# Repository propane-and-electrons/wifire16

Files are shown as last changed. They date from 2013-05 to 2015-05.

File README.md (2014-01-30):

wifire16
--------

After I wired up 16 MOSFET + optoisolator circuits on perfboard for Flux and Fire, I swore I was never going to do it by hand again. When it came time to make a similar circuit for Super Street Fire, I decided the only option was to make a PCB to wirelessly control 16 flame effects. The end result: the wifire16 board.

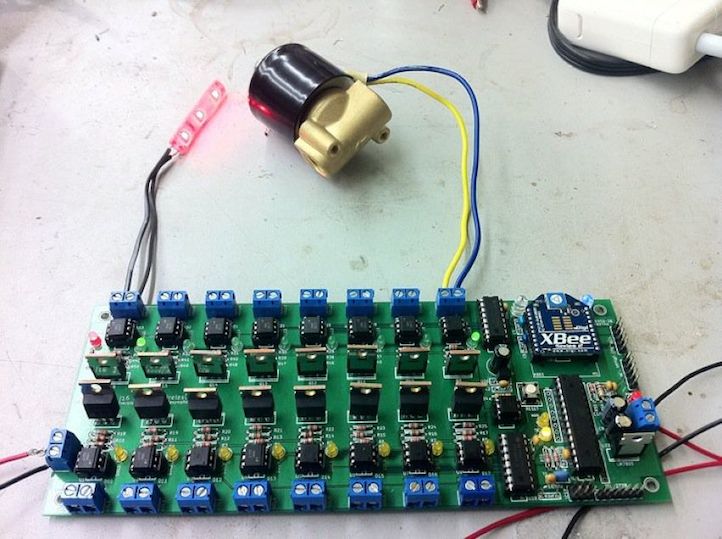
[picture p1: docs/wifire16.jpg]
wifire16 photo


### Feature Summary

* Arduino compatible
* Programmable via 6-pin FTDI header or 6-pin ICSP header
* 16 PWM-capable DC load channels switched via MOSFET
* Wireless support with XBee or compatible radio, e.g. RN-XV WiFly
* All ATMega I/O pins are broken out on the board
* DC load power is optoisolated from the control system power
* Power connectors use 5mm screw terminals or Anderson Powerpole connectors
* Load power status is reported to the microcontroller via an optoisolated input pin
* Output power channels are controlled with a TLC5940 constant current driver that works like a shift register
* Each output channel has a status LED for easy debugging
* TLC5940 control lines are broken out to input/output headers, so boards can be chained without additional control systems

### Design

The wifire16 takes two power inputs: 7-12 volts for the control side, and anything (within reason, e.g. 12 or 24 volts) for the load side. The control system acts exactly like an Arduino with attached XBee/WiFly radio, and is electrically optoisolated from the load side.The independent microcontroller (ATMega328P) on the board can control the power output channels via a pre-programmed routine, interactively over a wireless link, or with external sensors attached to the I/O pins. If more than 16 channels are needed, multiple boards can be chained together and controlled in the same way, with only one control system necessary.

The original purpose of the wifire16 is to control DC-powered solenoid valves for flame effects. The isolation of the two power sources protects the control side from the higher voltage load side, and also allows the load side power to be cut (i.e. by an arming or deadman switch) without affecting the control system. While the system was intended to handle solenoid valves that require 1A+ per channel, it can also be used to control anything else that needs DC power, e.g. motors or 12v LED rope lighting.

### v1 Note

The deprecated v1 version of this board used regular 74595 shift registers and were not PWM capable on all output channels. It also did not have Anderson Powerpole connnectors.

### Documents

* [Schematic](docs/wifire16-schematic.pdf)
* [Bill of Materials](docs/wifire16-BOM.csv)

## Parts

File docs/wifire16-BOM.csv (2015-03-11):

Designator | Package | Quantity | Part | Digi-Key Part
C1,C2,C3,C4,C6,C11 | C2 | 6 | 0.1uF | 490-5388-ND
C5 | C1V8 | 1 | 100uF | P13459-ND
C7,C12,C13 | C2 | 3 | 1uF | 445-2858-ND
C8 | C2 | 1 | 8.2pF | 490-3764-ND
C9,C10 | C1V5 | 2 | 47uF | P13464-ND
D2,D4,D6,D8,D10,D12,D14,D16,D18,D20,D22,D24,D26,D28,D30,D32,D33 | LED-3MM | 17 | LED 3mm (red) | 754-1606-ND
D1,D3,D5,D7,D9,D11,D13,D15,D17,D19,D21,D23,D25,D27,D29,D31,D34 | D3 | 17 | 1N4004 | 641-1311-1-ND
D35,D36,D37 | LED-3MM | 3 | LED 3mm (green) | 754-1603-ND
JP1,JP2,P20 | SIL-2, SIL-6 | 10 | header pins | A34253-40-ND
M1 | XBEE | 1 | RN-XV | 740-1044-ND
P1-P17,P27 | PP-2H-5MMSCREWTERM | 18 | 5mm screw terminals or Anderson Powerpole connectors | ED2600-ND
P21 | pin_array_3x2 | 3 | 2x header pins | A34344-40-ND
Q1-Q17 | TO220GDS_VERT | 16 | IRF510 | IRF510PBF-ND
R1,R3,R5,R7,R9,R11,R13,R15,R17,R19,R21,R23,R25,R27,R29,R31,R36 | R3 | 17 | 10k | 10KQBK-ND
R2,R4,R6,R8,R10,R12,R14,R16,R18,R20,R22,R24,R26,R28,R30,R32,R34,R37,R38,R39 | R3 | 20 | 1k | 1.0KQBK-ND
R33 | R3 | 1 | 2.2k | 2.2QBK-ND
R35 | R3 | 1 | 4k | not in stock?!
SW1 | SW-6MM-4PIN | 1 | momentary pushbutton | SW400-ND
U1-U17 | DIP-6__300 | 17 | 4N35 | 516-1557-5-ND
U18 | DIP-28__300 | 1 | TLC5940 | 296-17732-5-ND
U19 | SIL-3 | 1 | MCP1700 | MCP1700-3302E/TO-ND
U20 | DIP-14__300 | 1 | 74AHC125 | 296-4531-5-ND
U21 | 7805 | 1 | LM7805 | LM7805CT-ND
U22 | DIP-28__300 | 1 | ATMEGA328 | ATMEGA328P-PU-ND
U23 | SIL-3 | 1 | MCP1702 | MCP1702-1502E/TO-ND
XM1A,XM1B |  | 2 | 10pin 2mm header | S5751-10-ND
XU1-XU17 | 6-DIP | 17 | 6-DIP socket | A100203-ND
Y1 | SIL-3 | 1 | 16MHz | 490-1214-ND

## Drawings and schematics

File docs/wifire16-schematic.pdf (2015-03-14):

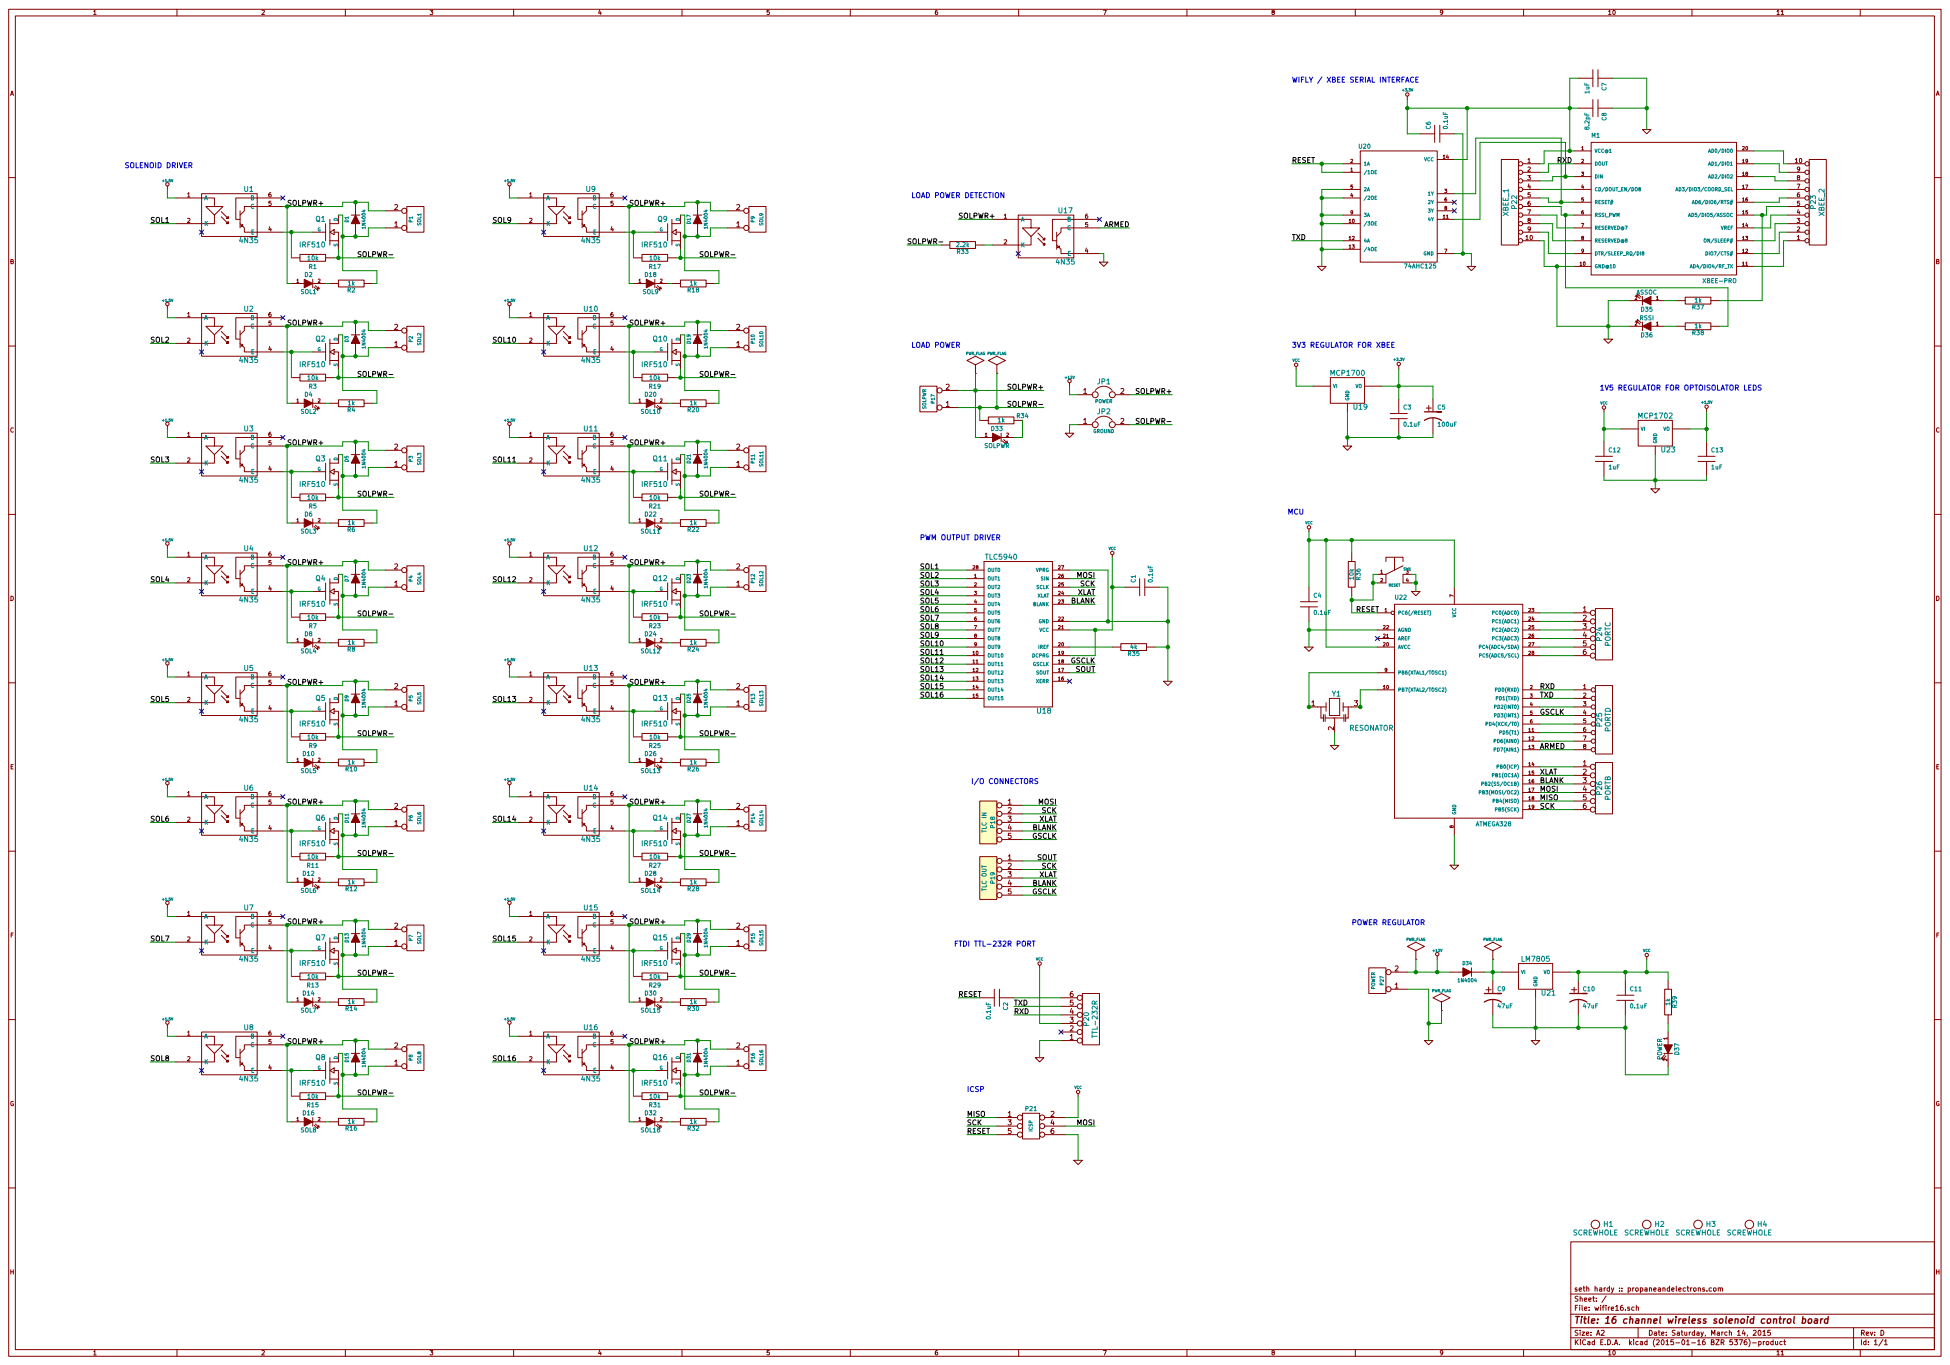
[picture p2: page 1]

WIFLY / XBEE SERIAL INTERFACE

1V5 REGULATOR FOR OPTOISOLATOR LEDS

H4 SCREWHOLE H3 SCREWHOLE H2 SCREWHOLE H1 SCREWHOLE

File: wifire16.sch Sheet: / seth hardy :: propaneandelectrons.com

Id: 1/1 Title: 16 channel wireless solenoid control board

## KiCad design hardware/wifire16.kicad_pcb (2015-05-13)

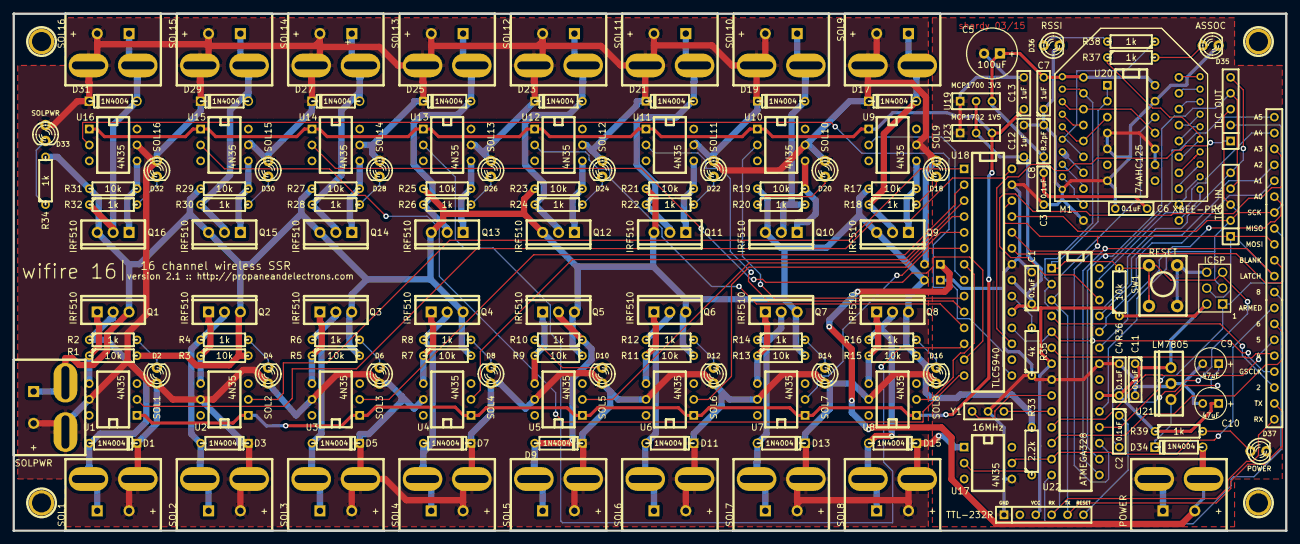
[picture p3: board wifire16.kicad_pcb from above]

Board: 2 copper layers, 203.2 x 82.5 mm, 164 parts (0 on the bottom side), 120 nets.

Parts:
C1, C2, C3, C4, C6, C11: 0.1uF; C2
C5: 100uF; C1V8
C7, C12, C13: 1uF; C2
C8: 8.2pF; C2
C9, C10: 47uF; C1V5
D1, D3, D5, D7, D9, D11, D13, D15, D17, D19, D21, D23, D25, D27, D29, D31, D34: 1N4004; D3
D2: SOL1; LED-3MM
D4: SOL2; LED-3MM
D6: SOL3; LED-3MM
D8: SOL4; LED-3MM
D10: SOL5; LED-3MM
D12: SOL6; LED-3MM
D14: SOL7; LED-3MM
D16: SOL8; LED-3MM
D18: SOL9; LED-3MM
D20: SOL10; LED-3MM
D22: SOL11; LED-3MM
D24: SOL12; LED-3MM
D26: SOL13; LED-3MM
D28: SOL14; LED-3MM
D30: SOL15; LED-3MM
D32: SOL16; LED-3MM
D33: SOLPWR; LED-3MM
D35: ASSOC; LED-3MM
D36: RSSI; LED-3MM
D37: POWER; LED-3MM
H1, H2, H3, H4: SCREWHOLE; 1pin
JP1: POWER; SIL-2
JP2: GROUND; SIL-2
M1: XBEE-PRO; XBEE
P1: SOL1; PP-2H-5MMSCREWTERM
P2: SOL2; PP-2H-5MMSCREWTERM
P3: SOL3; PP-2H-5MMSCREWTERM
P4: SOL4; PP-2H-5MMSCREWTERM
P5: SOL5; PP-2H-5MMSCREWTERM
P6: SOL6; PP-2H-5MMSCREWTERM
P7: SOL7; PP-2H-5MMSCREWTERM
P8: SOL8; PP-2H-5MMSCREWTERM
P9: SOL9; PP-2H-5MMSCREWTERM
P10: SOL10; PP-2H-5MMSCREWTERM
P11: SOL11; PP-2H-5MMSCREWTERM
P12: SOL12; PP-2H-5MMSCREWTERM
P13: SOL13; PP-2H-5MMSCREWTERM
P14: SOL14; PP-2H-5MMSCREWTERM
P15: SOL15; PP-2H-5MMSCREWTERM
P16: SOL16; PP-2H-5MMSCREWTERM
P17: SOLPWR; PP-2H-5MMSCREWTERM
P18: TLC IN; SIL-5
P19: TLC OUT; SIL-5
P20: TTL-232R; SIL-6
P21: ICSP; pin_array_3x2
P22: XBEE_1; SIL-10
P23: XBEE_2; SIL-10
P24: PORTC; SIL-6
P25: PORTD; SIL-8
P26: PORTB; SIL-6
P27: POWER; PP-2H-5MMSCREWTERM
Q1, Q2, Q3, Q4, Q5, Q6, Q7, Q8, Q9, Q10, Q11, Q12, Q13, Q14, Q15, Q16: IRF510; TO220GDS_VERT
R1, R3, R5, R7, R9, R11, R13, R15, R17, R19, R21, R23, R25, R27, R29, R31, R36: 10k; R3
R2, R4, R6, R8, R10, R12, R14, R16, R18, R20, R22, R24, R26, R28, R30, R32, R34, R37, R38, R39: 1k; R3
R33: 2.2k; R3
R35: 4k; R3
SW1: RESET; SW-6MM-4PIN
U1, U2, U3, U4, U5, U6, U7, U8, U9, U10, U11, U12, U13, U14, U15, U16, U17: 4N35; DIP-6__300
U18: TLC5940; DIP-28__300
U19: MCP1700 3V3; SIL-3
U20: 74AHC125; DIP-14__300
U21: LM7805; 7805
U22: ATMEGA328; DIP-28__300
U23: MCP1702 1V5; SIL-3
Y1: 16MHz; SIL-3

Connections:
+1.5V: C13.1, U1.1, U2.1, U3.1, U4.1, U5.1, U6.1, U7.1, U8.1, U9.1, U10.1, U11.1, U12.1, U13.1, U14.1, U15.1, U16.1, U23.3
+3.3V: C3.1, C5.1, C6.1, C7.2, C8.2, M1.1, P22.1, U19.3, U20.14
+12V: D34.1, JP1.1, P27.2
/ARMED: P25.8, U17.5, U22.13
/BLANK: P18.4, P19.4, P26.3, U18.23, U22.16
/GSCLK: P18.5, P19.5, P25.4, U18.18, U22.5
/MISO: P21.1, P26.5, U22.18
/MOSI: P18.1, P21.4, P26.4, U18.26, U22.17
/RESET: C2.2, P21.5, R36.2, SW1.1, SW1.2, U20.1, U20.2, U22.1
/RXD: M1.2, P20.4, P22.2, P25.1, U22.2
/SCK: P18.2, P19.2, P21.3, P26.6, U18.25, U22.19
/SOL1: U1.2, U18.28
/SOL2: U2.2, U18.1
/SOL3: U3.2, U18.2
/SOL4: U4.2, U18.3
/SOL5: U5.2, U18.4
/SOL6: U6.2, U18.5
/SOL7: U7.2, U18.6
/SOL8: U8.2, U18.7
/SOL9: U9.2, U18.8
/SOL10: U10.2, U18.9
/SOL11: U11.2, U18.10
/SOL12: U12.2, U18.11
/SOL13: U13.2, U18.12
/SOL14: U14.2, U18.13
/SOL15: U15.2, U18.14
/SOL16: U16.2, U18.15
/SOLPWR+: D1.2, D2.1, D3.2, D4.1, D5.2, D6.1, D7.2, D8.1, D9.2, D10.1, D11.2, D12.1, D13.2, D14.1, D15.2, D16.1, D17.2, D18.1, D19.2, D20.1, D21.2, D22.1, D23.2, D24.1, D25.2, D26.1, D27.2, D28.1, D29.2, D30.1, D31.2, D32.1, D33.1, JP1.2, P1.2, P2.2, P3.2, P4.2, P5.2, P6.2, P7.2, P8.2, P9.2, P10.2, P11.2, P12.2, P13.2, P14.2, P15.2, P16.2, P17.2, U1.5, U2.5, U3.5, U4.5, U5.5, U6.5, U7.5, U8.5, U9.5, U10.5, U11.5, U12.5, U13.5, U14.5, U15.5, U16.5, U17.1
/SOLPWR-: JP2.2, P17.1, Q1.S, Q2.S, Q3.S, Q4.S, Q5.S, Q6.S, Q7.S, Q8.S, Q9.S, Q10.S, Q11.S, Q12.S, Q13.S, Q14.S, Q15.S, Q16.S, R1.2, R3.2, R5.2, R7.2, R9.2, R11.2, R13.2, R15.2, R17.2, R19.2, R21.2, R23.2, R25.2, R27.2, R29.2, R31.2, R33.2, R34.2
/SOUT: P19.1, U18.17
/TXD: P20.5, P25.2, U20.12, U22.3
/XLAT: P18.3, P19.3, P26.2, U18.24, U22.15
GND: C1.2, C3.2, C4.2, C5.2, C6.2, C7.1, C8.1, C9.2, C10.2, C11.2, C12.2, C13.2, D35.2, D36.2, D37.2, JP2.1, M1.10, P20.1, P21.6, P22.10, P27.1, R35.1, SW1.3, SW1.4, U17.4, U18.22, U18.27, U19.1, U20.4, U20.5, U20.7, U20.9, U20.10, U20.13, U21.2, U22.8, U22.22, U23.1, Y1.2
unnamed: C2.1, P20.6
unnamed: C9.1, D34.2, U21.1
unnamed: D1.1, P1.1, Q1.D, R2.1
unnamed: D2.2, R2.2
unnamed: D3.1, P2.1, Q2.D, R4.1
unnamed: D4.2, R4.2
unnamed: D5.1, P3.1, Q3.D, R6.1
unnamed: D6.2, R6.2
unnamed: D7.1, P4.1, Q4.D, R8.1
unnamed: D8.2, R8.2
unnamed: D9.1, P5.1, Q5.D, R10.1
unnamed: D10.2, R10.2
unnamed: D11.1, P6.1, Q6.D, R12.1
unnamed: D12.2, R12.2
unnamed: D13.1, P7.1, Q7.D, R14.1
unnamed: D14.2, R14.2
unnamed: D15.1, P8.1, Q8.D, R16.1
unnamed: D16.2, R16.2
unnamed: D17.1, P9.1, Q9.D, R18.1
unnamed: D18.2, R18.2
unnamed: D19.1, P10.1, Q10.D, R20.1
unnamed: D20.2, R20.2
unnamed: D21.1, P11.1, Q11.D, R22.1
unnamed: D22.2, R22.2
unnamed: D23.1, P12.1, Q12.D, R24.1
unnamed: D24.2, R24.2
unnamed: D25.1, P13.1, Q13.D, R26.1
unnamed: D26.2, R26.2
unnamed: D27.1, P14.1, Q14.D, R28.1
unnamed: D28.2, R28.2
unnamed: D29.1, P15.1, Q15.D, R30.1
unnamed: D30.2, R30.2
unnamed: D31.1, P16.1, Q16.D, R32.1
unnamed: D32.2, R32.2
unnamed: D33.2, R34.1
unnamed: D35.1, R37.2
unnamed: D36.1, R38.2
unnamed: D37.1, R39.2
unnamed: M1.3, P22.3, U20.11
unnamed: M1.4, P22.4
unnamed: M1.5, P22.5, U20.3
unnamed: M1.6, P22.6, R38.1
unnamed: M1.7, P22.7
unnamed: M1.8, P22.8
unnamed: M1.9, P22.9
unnamed: M1.11, P23.1
unnamed: M1.12, P23.2
unnamed: M1.13, P23.3
unnamed: M1.14, P23.4
unnamed: M1.15, P23.5, R37.1
unnamed: M1.16, P23.6
unnamed: M1.17, P23.7
unnamed: M1.18, P23.8
unnamed: M1.19, P23.9
unnamed: M1.20, P23.10
unnamed: P24.1, U22.23
unnamed: P24.2, U22.24
unnamed: P24.3, U22.25
unnamed: P24.4, U22.26
unnamed: P24.5, U22.27
unnamed: P24.6, U22.28
unnamed: P25.3, U22.4
unnamed: P25.5, U22.6
unnamed: P25.6, U22.11
unnamed: P25.7, U22.12
unnamed: P26.1, U22.14
unnamed: Q1.G, R1.1, U1.4
unnamed: Q2.G, R3.1, U2.4
unnamed: Q3.G, R5.1, U3.4
unnamed: Q4.G, R7.1, U4.4
unnamed: Q5.G, R9.1, U5.4
unnamed: Q6.G, R11.1, U6.4
unnamed: Q7.G, R13.1, U7.4
unnamed: Q8.G, R15.1, U8.4
unnamed: Q9.G, R17.1, U9.4
unnamed: Q10.G, R19.1, U10.4
unnamed: Q11.G, R21.1, U11.4
unnamed: Q12.G, R23.1, U12.4
unnamed: Q13.G, R25.1, U13.4
unnamed: Q14.G, R27.1, U14.4
unnamed: Q15.G, R29.1, U15.4
unnamed: Q16.G, R31.1, U16.4
unnamed: R33.1, U17.2
unnamed: R35.2, U18.20
unnamed: U22.9, Y1.1
unnamed: U22.10, Y1.3
VCC: C1.1, C4.1, C10.1, C11.1, C12.1, P20.3, P21.2, R36.1, R39.1, U18.19, U18.21, U19.2, U21.3, U22.7, U22.20, U23.2

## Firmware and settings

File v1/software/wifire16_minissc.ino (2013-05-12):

// simple program to run a wifire16 v1 board off a MiniSSC relay controller

#include <SPI.h>

// pin definitions
#define CLEARPIN 4    // master clear for 74HC595 shift registers
#define LATCHPIN 5    // latch for 74HC595 shift registers
#define OEPIN    6    // output enable for 74HC595 shift registers
#define ARMEDPIN 7    // optoisolator connected to load power
#define DATAPIN  11   // data for 74HC595 shift registers
#define CLOCKPIN 13   // clock for 74HC595 shift registers 

#define bitFlip(x,n)  bitRead(x,n) ? bitClear(x,n) : bitSet(x,n)

byte c;
byte v;
byte r1 = 0, r2 = 0;

// setup
void setup() {
  
  // set all output pins
  SPI.begin(); // handles DATAPIN and CLOCKPIN
  pinMode(LATCHPIN, OUTPUT);
  pinMode(OEPIN, OUTPUT);
  pinMode(CLEARPIN, OUTPUT);

  // make sure no lines go active until data is shifted out
  digitalWrite(CLEARPIN, HIGH);
  digitalWrite(OEPIN, LOW);

  // clear any lines that were left active
  digitalWrite(LATCHPIN, LOW);
  digitalWrite(OEPIN, HIGH);
  c = SPI.transfer(0);
  c = SPI.transfer(0);
  digitalWrite(LATCHPIN, HIGH);
  digitalWrite(OEPIN, LOW);
  
  // activate built-in pull-up resistor 
  digitalWrite(ARMEDPIN, HIGH);

  // start the serial communication with the xbee
  Serial.begin(115200);

}


// main loop
void loop() {

  if(Serial.available() >= 3) {
    c = Serial.read();
    if(c == 0xFF) {
      c = Serial.read();
      if( (c >= 0) && (c <= 0x0f) ) {
        v = Serial.read();
        if(v == 0) {
          if(c > 7) {
            bitClear(r2,c-8);
          }
          else {
            bitClear(r1,c);
          }
        }
        else if(v == 1) {
          if(c > 7) {
            bitSet(r2,c-8);
          }
          else {
            bitSet(r1,c);
          }
        }
        if((v == 0) || (v == 1)) {
          digitalWrite(LATCHPIN, LOW);
          digitalWrite(OEPIN, HIGH);
          c = SPI.transfer(r2);
          c = SPI.transfer(r1);
          digitalWrite(LATCHPIN, HIGH);
          digitalWrite(OEPIN, LOW);
        }
      }
    }
  }
}

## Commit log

2013-03-26 initial commit - need to clean this up, but at least getting it into the repo
    [wifire16.brd, wifire16.dsn, wifire16.sch]
2013-05-12 minissc relay script
2014-01-05 moving things around
    [wifire16.brd, wifire16.dsn, wifire16.sch]
2014-01-05 2.0 revisions - swapped powerpole direction (and diodes), backannotated schematic with footprints, other fixups
    [wifire16.brd, wifire16.sch]
2014-01-05 a few more file changes
    [wifire16.brd, wifire16.dsn, wifire16.sch]
2014-01-05 adding documentation
    [wifire16-BOM.csv]
2015-03-11 fixing bugs, using a new version of kicad
    [wifire16.brd, wifire16.kicad_pcb, wifire16.sch]
2015-03-11 updating to 2.1 docs
    [wifire16-BOM.csv]
2015-03-14 removing unused pin name
    [wifire16.kicad_pcb, wifire16.sch]
2015-05-13 fixing zone clearances
    [wifire16.kicad_pcb]
